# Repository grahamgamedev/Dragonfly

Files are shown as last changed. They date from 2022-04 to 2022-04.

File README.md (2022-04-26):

# Dragonfly
434mm aluminium quadcopter frame (8 inch props)
## Discription
- FCStd contains design files in FreeCAD and LibreCAD format
- STL contains the STL flies for 3D printing and the PDF file for 2D printing
- Prams.md contains most of the custom pramiters for Ardupilot

## Required tools
- 3D printer
- 2D printer
- Sicsors
- Glue stick (to stick down templates)
- Tape mesure
- Tri-square
- Small nail (to mark aluminium)
- Hacksaw
- Dril
- 5mm drill bit
- 3.5mm drill bit
- Wet and dry paper
- M3 tap drill
- Screwdriver
- 8mm socket and ratchet
- 3mm hex key 
- Soldering iron
- Tweezers

## Optional but highly recomended tools
- Piller dril
- Center punch
- Metel file

## Ground Hardware
- Radio transmitter
- 18650 cells (for transmitter)
- Battery charger (up to 6S LiPo)
- Fire proof charging bag

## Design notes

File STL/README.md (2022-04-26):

# Print Settings
All 3D prints done on my Ender 3 Pro.
0.8mm nozzle is optional but speeds up the process.

## FC Mount.stl
- Nozzle size = 0.4mm
- Infill = 10%
- No Top Layers
- Support = no
- Brim = no
- Material = PLA
- Color = black
- Quantity = 1

## GPS Cable Cover.stl
- Nozzle size = 0.4mm
- Infill = Any
- Support = no
- Brim = yes
- Material = PLA
- Color = black
- Quantity = 1

## Lid.stl
- Nozzle size = 0.4mm
- Infill = Any
- Support = yes
- Brim = yes
- Material = PLA
- Color = red
- Quantity = 1

## Battery Holder.stl
- Nozzle size = 0.8mm
- Infill = 20%
- Support = yes
- Brim = no
- Material = PLA
- Color = red
- Quantity = 1

## Leg Bracket.stl
- Nozzle size = 0.8mm
- Infill = Any
- Support = no
- Brim = yes
- Material = PLA
- Color = black
- Quantity = 8

## Release.stl
- Nozzle size = 0.8mm
- Infill = 20%
- Support = no
- Brim = no
- Material = PLA
- Color = red
- Quantity = 1

## Foot.stl
- Nozzle size = 0.4mm
- Infill = 50%
- Support = no
- Brim = no
- Material = PLA
- Color = black
- Quantity = 4

## Frame Templates.pdf
- Paper size = A4
- Duplex = no
- Color = yes
- Quantity = 2

## logo.png
- Paper size = Avery Label J8163
- Duplex = no
- Color = yes
- Quantity = 2

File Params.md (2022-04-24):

# Ardupilot Params

## Telem2
SERIAL2_PROTOCALL=10
SERIAL2_OPTIONS=7

Tlem2 TX --> SPort

## Switches
RC8_OPTION=19
RC9_OPTION=153

## Gripper
GRIP_ENABLE=1
GRIP_TYPE=1
GRIP_GRAB=
GRIP_RELEASE=
GRIP_NEUTRAL=

## Battery Monitor
BATT_CRT_MAH=1000
BATT_CRT_VOLT=19
BATT_CURR_PIN=10
BATT_FS_CRT_ACT=1
BATT_FS_LOW_ACT=2
BATT_LOW_MAH=2000
BATT_LOW_VOLT=20
BATT_VOLT_PIN=13
FS_OPTIONS=24

## Tuning
RTL_ALT=20
ANGLE_MAX=4000
LOIT_ANG_MAX=40

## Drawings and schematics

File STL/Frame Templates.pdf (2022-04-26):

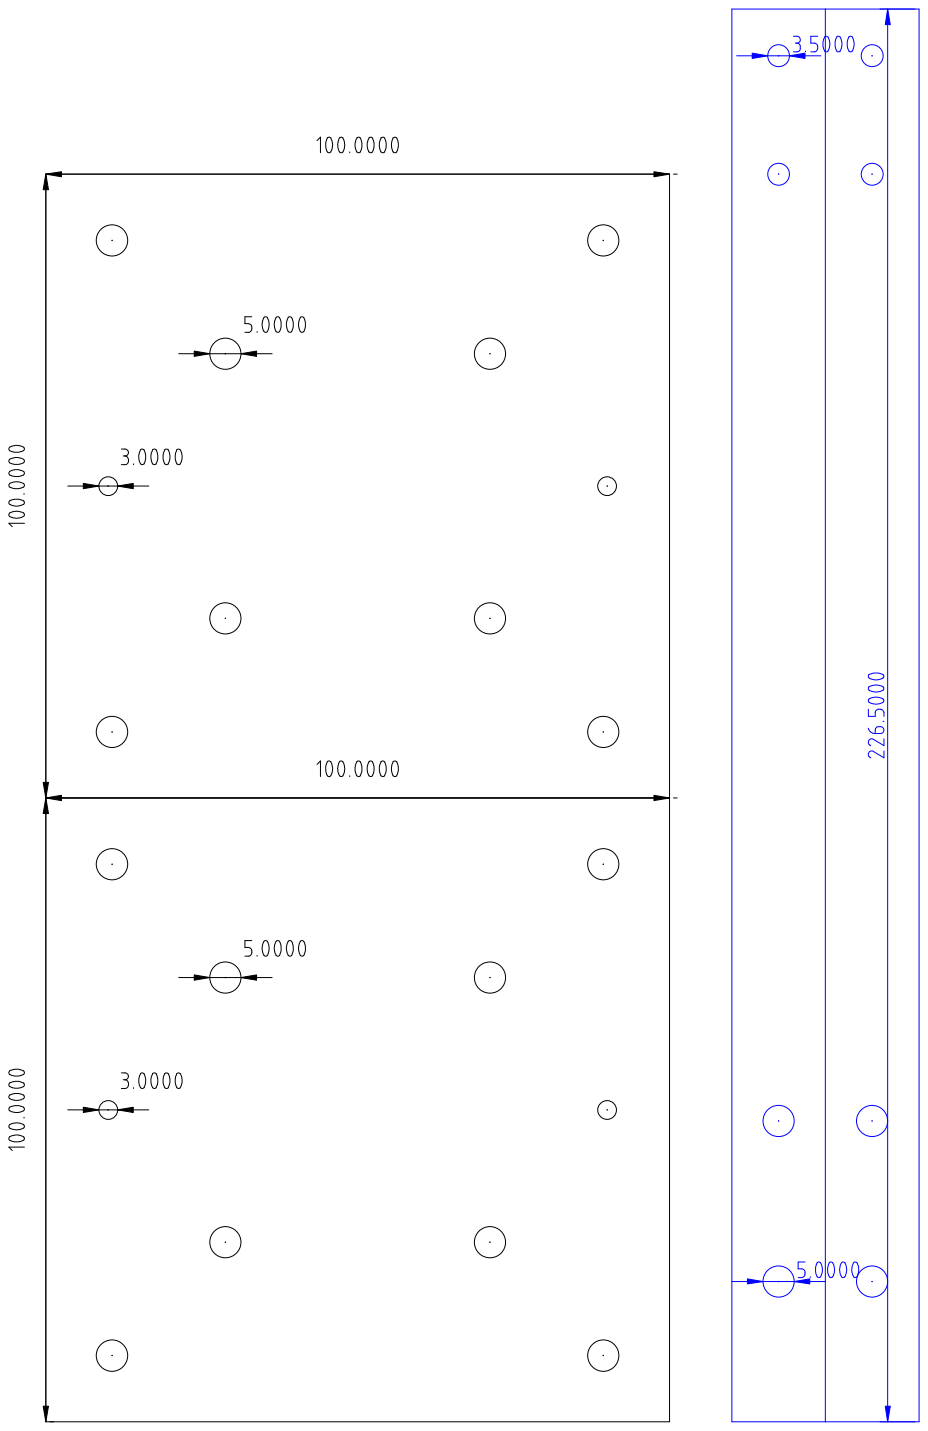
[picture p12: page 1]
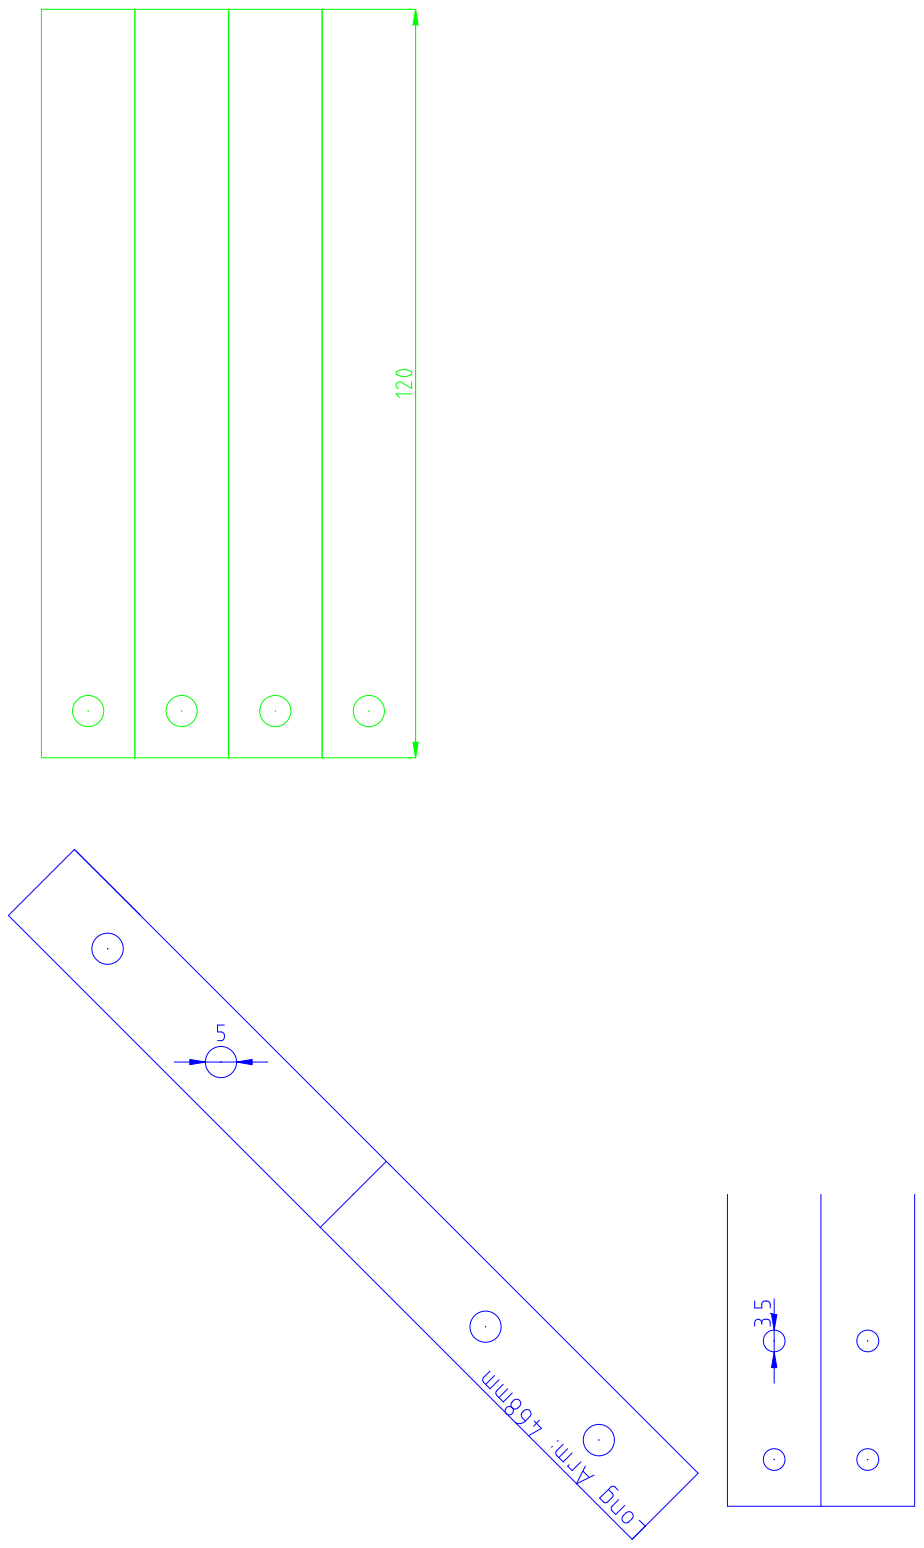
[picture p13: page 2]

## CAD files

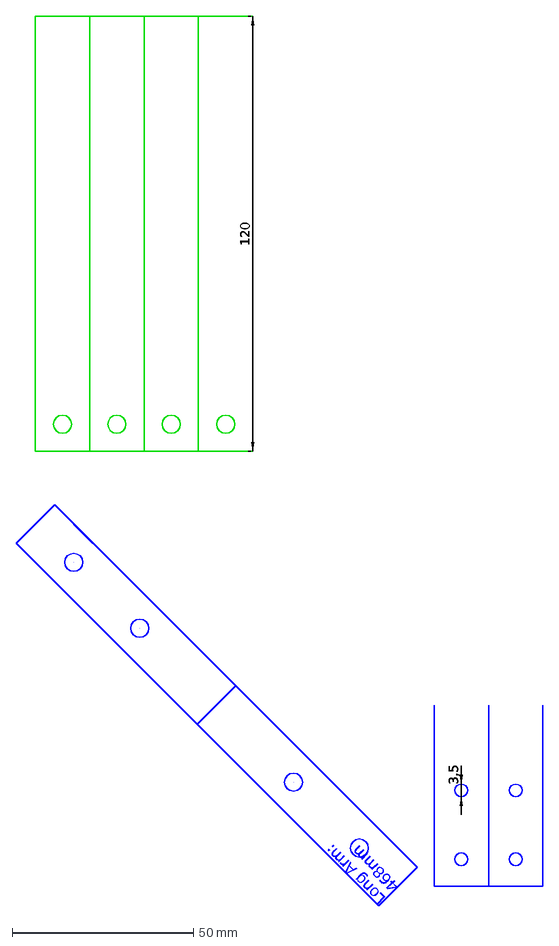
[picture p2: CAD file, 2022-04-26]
FCStd/Frame Templates 2.dxf
3,5
120
Long Arm: 468mm

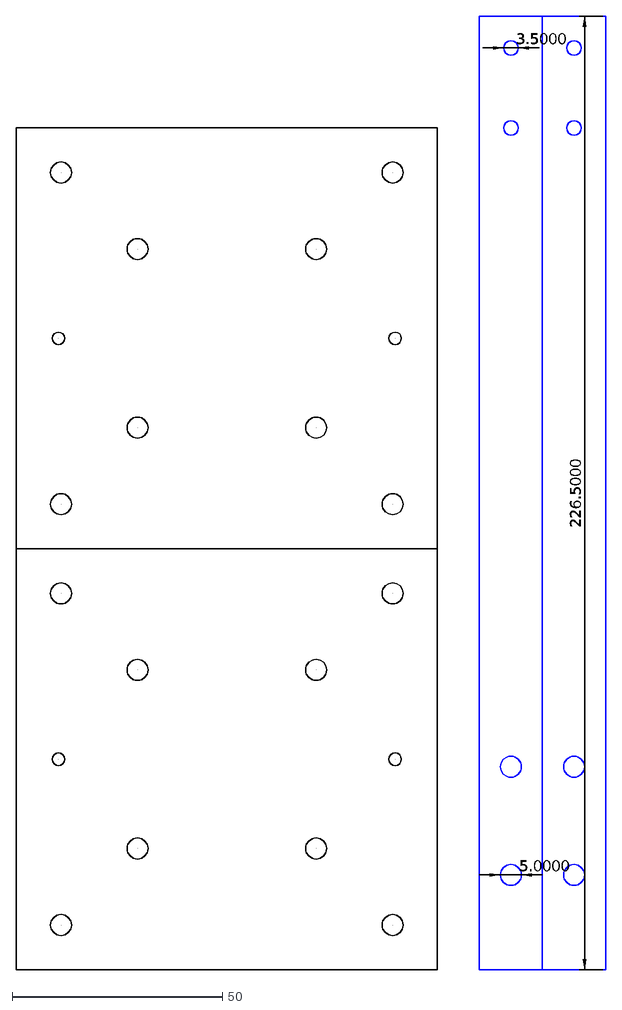
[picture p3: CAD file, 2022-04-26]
FCStd/Frame Templates 1.dxf
3.5000
5.0000
226.5000

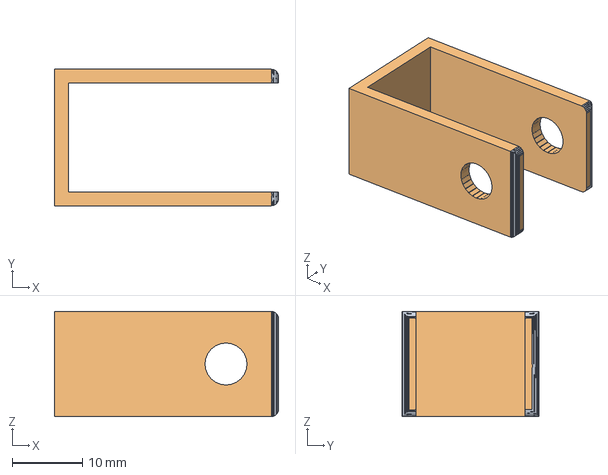
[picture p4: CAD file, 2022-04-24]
FCStd/Leg Bracket.FCStd
32.0 x 19.5 x 15.0 mm
Fillet (Meshed)

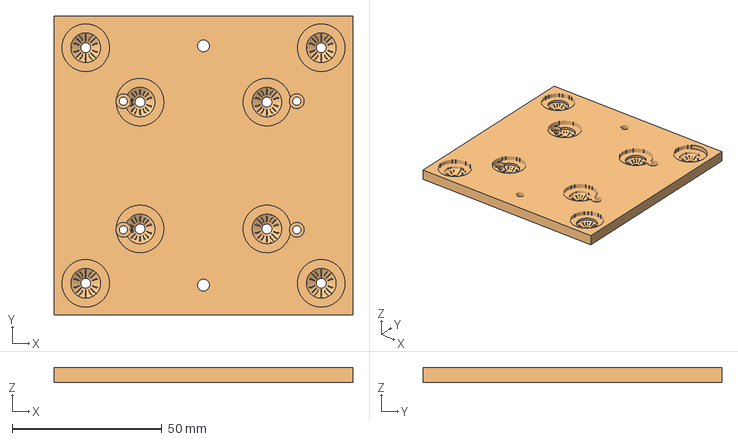
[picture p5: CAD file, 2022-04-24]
FCStd/FC Mount.FCStd
100.0 x 100.0 x 5.00 mm
Hole002 (Meshed)

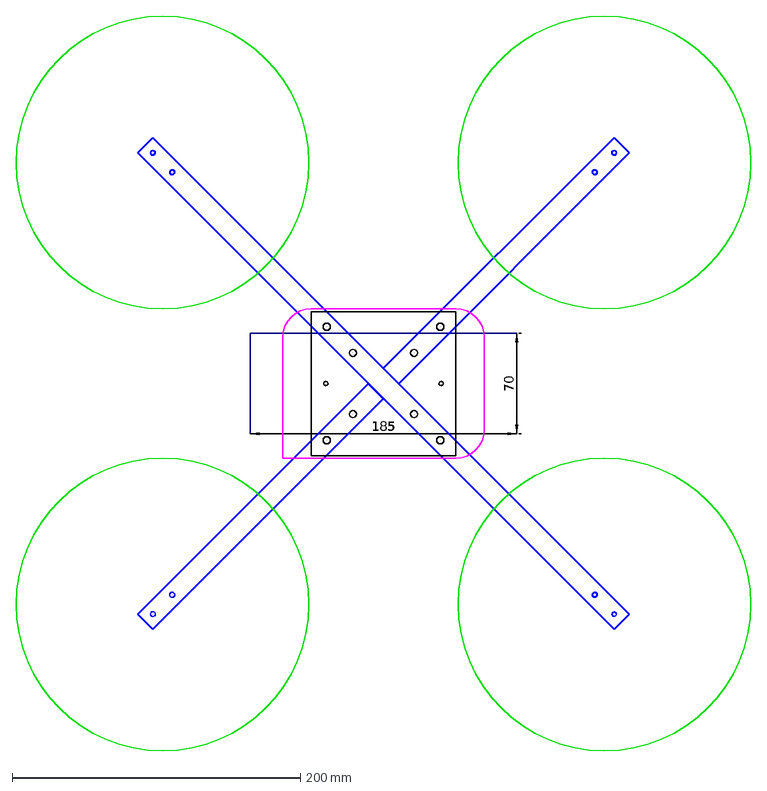
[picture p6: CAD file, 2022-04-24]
FCStd/Overvew.dxf
185
70

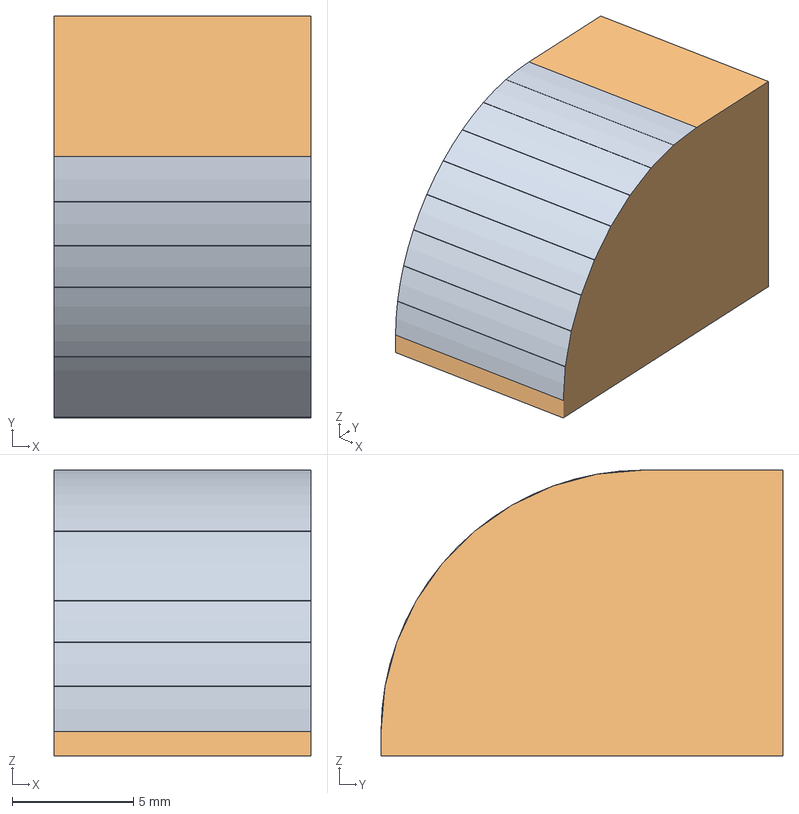
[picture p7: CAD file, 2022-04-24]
FCStd/GPS Cable Cover.FCStd
10.6 x 16.6 x 11.8 mm
Pocket (Meshed)

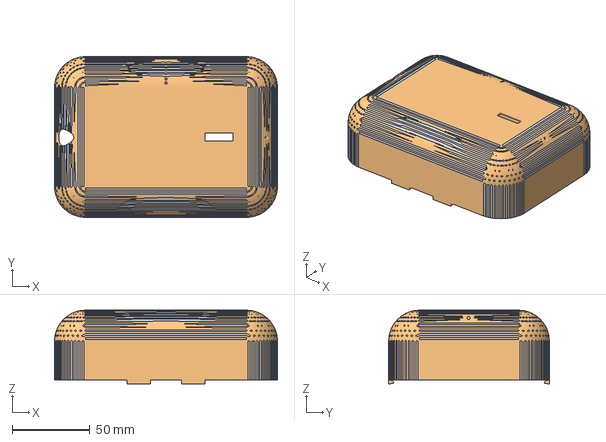
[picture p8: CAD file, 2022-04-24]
FCStd/Lid.FCStd
143.4 x 103.4 x 47.4 mm
Pocket002 (Meshed)

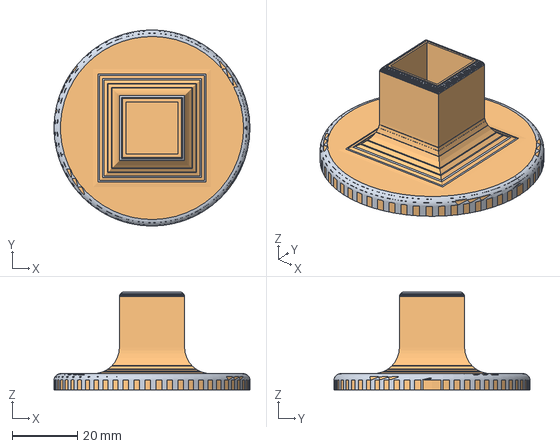
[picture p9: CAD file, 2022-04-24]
FCStd/Foot.FCStd
60.0 x 60.0 x 30.0 mm
Fillet002 (Meshed)

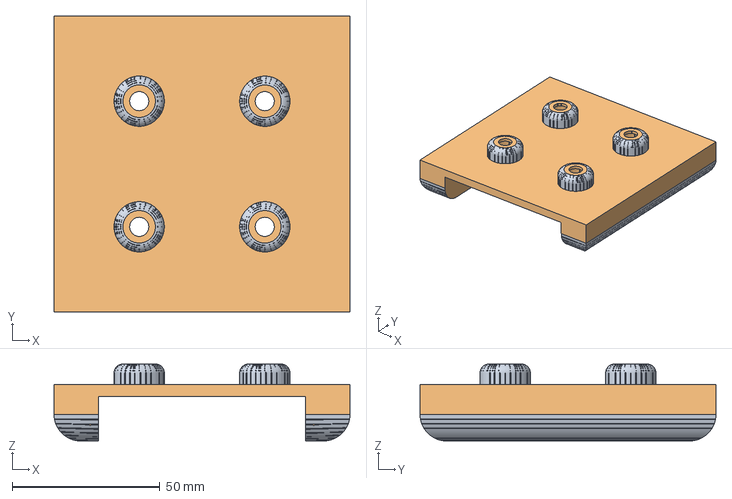
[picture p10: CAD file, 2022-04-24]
FCStd/Battery Holder.FCStd
100.0 x 100.0 x 26.0 mm
Fillet001 (Meshed)

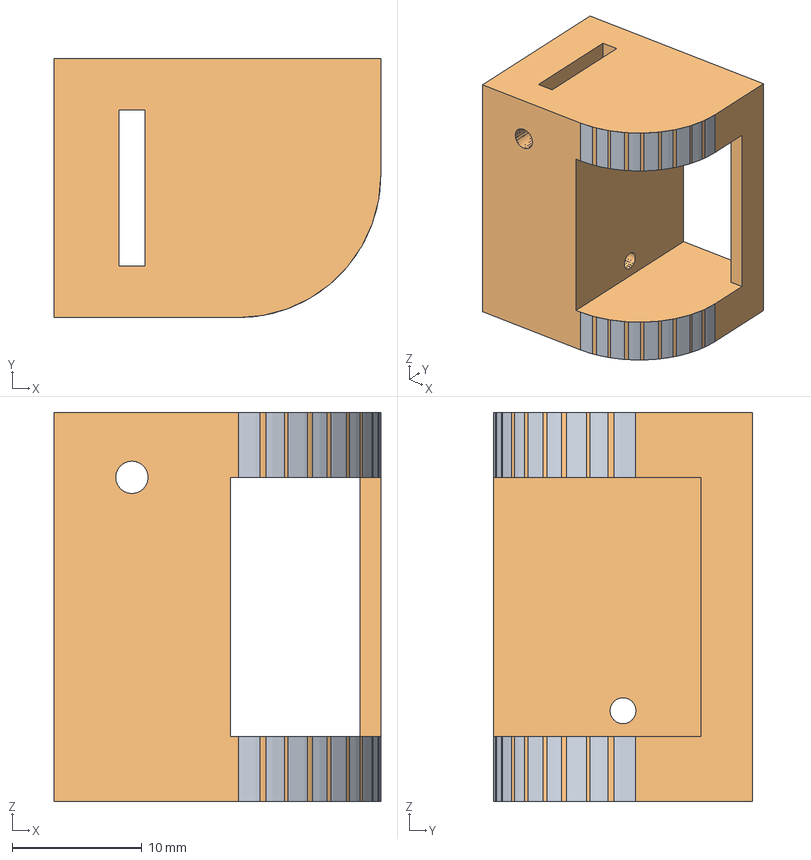
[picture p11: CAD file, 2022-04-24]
FCStd/Release.FCStd
25.2 x 20.0 x 30.0 mm
Hole002 (Meshed)

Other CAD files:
STL/Battery Holder.stl
STL/FC Mount.stl
STL/Foot.stl
STL/GPS Cable Cover.stl
STL/Leg Bracket.stl
STL/Lid.stl
STL/Release.stl
